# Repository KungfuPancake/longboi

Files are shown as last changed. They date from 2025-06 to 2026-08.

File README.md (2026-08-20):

# Longboi AFC controller
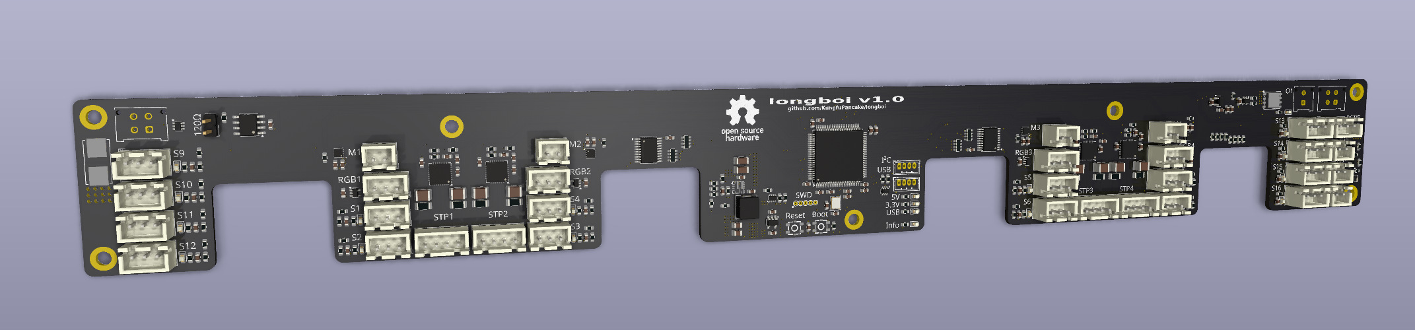
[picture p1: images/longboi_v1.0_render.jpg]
assembled pcb render

Tired of the mess of cables in your BoxTurtle? Want to add a heated filament dryer chamber some time down the road? Want to control that cooling fan with PWM? This project is for you!

The Longboi sits behind the full width of the BoxTurtle front panel and allows very short cable runs of equal length from each respooler and extruder. It's equipped with a beefy STM32H723 MCU and can be controlled with CAN or USB. If using CAN it's also daisy chainable for 8, 12 or even more lanes!

# How to get a Longboi

## Buying a complete board
LDO will sell complete boards via various resellers. Production is currently unknown - check back later for updates!

## PCB + Assembly by JLCPCB
You can order assembled PCBs from pretty much any fab, although currently only production files tested with JLCPCB are available in [jlcpcb/](https://github.com/KungfuPancake/longboi/tree/main/jlcpcb).
To order PCBs with assembly you'll have to go through their manufacturing wizard, using mostly standard settings. Although the JLC engineers will try and correct any mistakes, please do sanity checks on every page.
1. Upload `longboi.zip`into the PCB quote form and select a quantity. Five PCBs is the minimum quantity, cost per board will be lower the more boards you order since most of the cost is setup fees. Select a solder mask color you like - green is usually cheapest. I highly recommend choosing ENIG as a surface finish, HASL is usually not worth the saved money on production boards. Leave all other settings on their default values. Check PCBA (assembly) on the bottom of the form. Click "Next".
2. Check if the PCB looks like it should, then click "Next".
3. Upload `bom.csv` for BOM, `positions.csv`for CPL. Click "Next".
4. Check if all components look right, if there are stock shortages you will have to select replacement. Be very careful to select components that are equal or better in specs. If everything looks good, click "Next".
5. Check the placement of all components, especially if the first pin corresponds with the PCB markings. Slight inaccuracies on the big through hole connectors are okay, as they are hand soldered anyway. Click "Next".
6. You'll see a breakdown of all individual fees and prices. If you're flexible on the amount of PCBs you order you can try and see which amount has the best value to you.
7. Done!

Please be aware that the BOM only contains a fuse holder, the fuses (2410/1808) have to be sourced separately. 4A is a good value to start, depending on the heater you may or may not use the value can be scaled up or down accordingly.

## PCB + assembling it yourself
Order the PCBs anywere you want as the specs are very modest. Assembly of the board is an advanced task requiring lots of soldering, including hot air and/or using a reflow oven. If you don't feel comfortable with that, you should let the fab handle the assembly.

Please be aware that the BOM only contains a fuse holder, the fuses (2410/1808) have to be sourced separately. 4A is a good value to start, depending on the heater you may or may not use the value can be scaled up or down accordingly.

# Preparations
This is a general guideline how to proceed with flashing the Katapult bootloader (optional) and Klipper. If you struggle with the process or encounter errors on the way, especially when using CAN bus, try the detailed instructions and troubleshooting tips and tricks from [Esoterical's CANBus guide](https://canbus.esoterical.online/).
Start with only USB connected via the JST header. When plugging in the USB cable into your computer, the 3.3V and USB LEDs should light up. Now you're ready for flashing!

## CAN
### Katapult
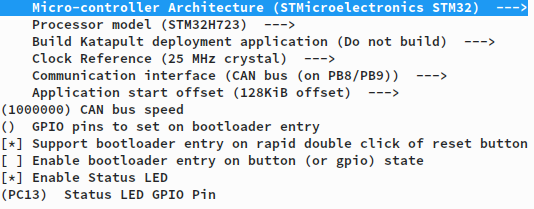
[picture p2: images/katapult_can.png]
katapult reference config for can


### Klipper
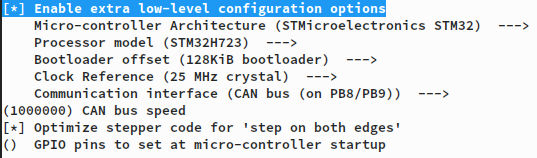
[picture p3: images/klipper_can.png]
klipper reference config for can


## USB
### Katapult
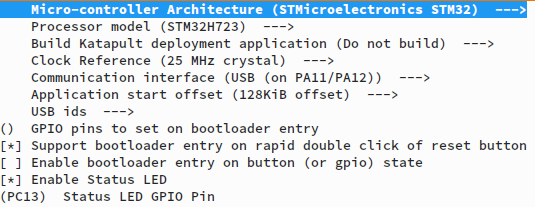
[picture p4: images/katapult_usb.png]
katapult reference config for usb


### Klipper
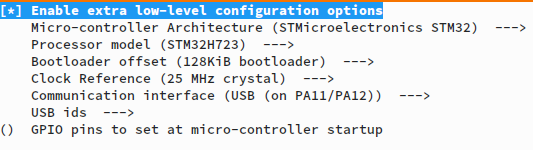
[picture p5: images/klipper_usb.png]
klipper reference config for usb


## Initial flash via DFU
To enable CAN or USB flashing via Katapult or Klipper you'll have to bootstrap the board via the MCUs built-in DFU bootloader, using dfu-util. To enter the DFU bootloader, hold down the "Boot"-button, then press the "Reset"-button shortly. You can now release both buttons and the Longboi should be visible as a "STM Device in DFU Mode" USB device.

Use dfu-util to flash the desired firmware, e.g. Katapult: ```dfu-util -R -a 0 -s 0x08000000:leave -D ~/katapult/out/katapult.bin -d 0483:df11```

## Flashing Katapult and/or Klipper
When using USB, flashing Katapult is not needed as Klipper can update its own firmware. Go through the Klipper build steps using the configuration from above, then flash klipper.bin using dfu-util. From now on you can update Klipper directly with ```make flash FLASH_DEVICE={your device path}```

If you're using a CAN setup and need to use Katapult, build it with the configuration from above and flash it via ```dfu-util```. You may have to reset the board with the "Reset"-button after flashing, the "Info"-LED should be blinking now. If it doesn't, try manually entering Katapult by double-clicking "Reset". Once Katapult is running, all flash operations have to be done via CAN bus. Remove the USB cable from the board and attach it to your CAN bus using a suitable cable. Remember to power down your printer before connecting anything!

If everything went well, Katapult should be visible with the flash tool: ```~/katapult/scripts/flashtool.py -i can0 -q```

You can now flash Klipper: ```~/katapult/scripts/flashtool.py -f ~/klipper/out/klipper.bin -u {your address}```

And you're done!

## Print parts
### Base BoxTurtle
BOM:
* ~95g of primary color filament
* 7x M3x4x5 heat set insert (Voron style)
* 7x M3x10 SHCS
* (Optional) 7x M3x5 brass standoffs
* (Optional) 7x M3x4 SHCS

Print the following parts in your primary color:

* 1x skirt_front_hex_single.stl (no split parts available yet)

If you're not using brass standoffs, also print:

* 7x pcb_spacer_x7.stl

Print all parts using the BoxTurtle settings, make sure that you tuned your filament for shrinkage as the mounting holes won't line up otherwise.

### BoxTurtle Enclosure
Please use the CAD files for reference until a detailed manual is available.

# Assembly
## Mounting PCB + front skirt
### Base BoxTurtle
Add the heat set inserts into the front skirt, then mount the PCB. If you're using brass standoffs, screw those in first, then mount the board using the M3x4 fasteners. If using printed spacers, for easier assembly you can pre-insert two M3x10s into the PCB, add spacers and then mount it on the front skirt. Then use tweezers to add spacers between the PCB and the skirt on the remaining holes and add the rest of the M3x10s.
Insert the front skirt according to the manual and double check that the cutouts on the PCB correspond to the respooler switch tabs.

### BoxTurtle Enclosure
Please use the CAD files for reference until a detailed manual is available.

## Connections
Every respooler + extruder has its own set of connectors on the PCB, e.g. M4, RGB4, S8, S7, STP4.
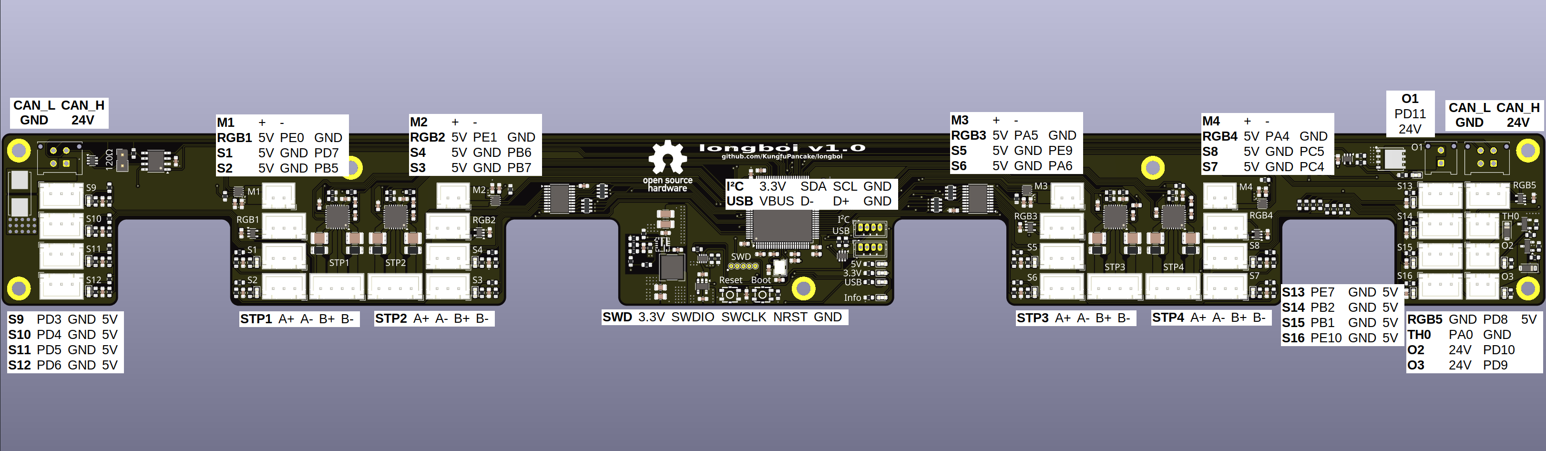
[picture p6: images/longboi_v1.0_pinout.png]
pcb 1.0 render with pinout

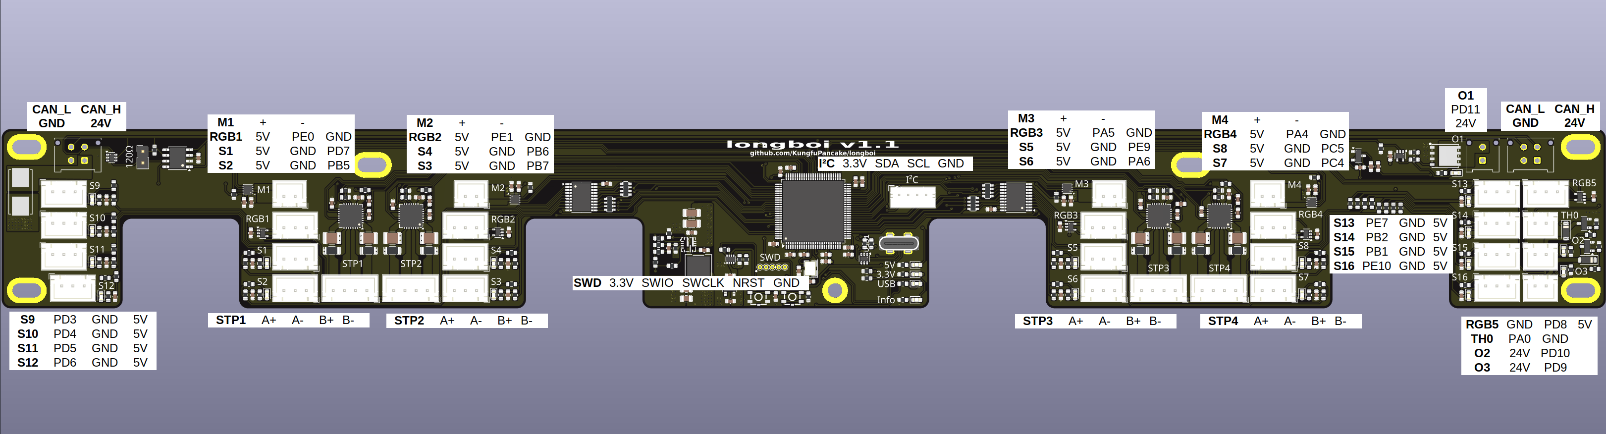
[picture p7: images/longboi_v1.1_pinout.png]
pcb 1.1 render with pinout


If you're making your own cables, to make your life easier, assemble one respooler and one extruder first with generous cable length. Mount everything, measure everything, cut and crimp all connections. Afterwards, remove the respooler and extruder and finish the other three sets outside of the BoxTurtle with your measurements.
Tidy up with cable ties/velcro straps as needed and plug in everything.
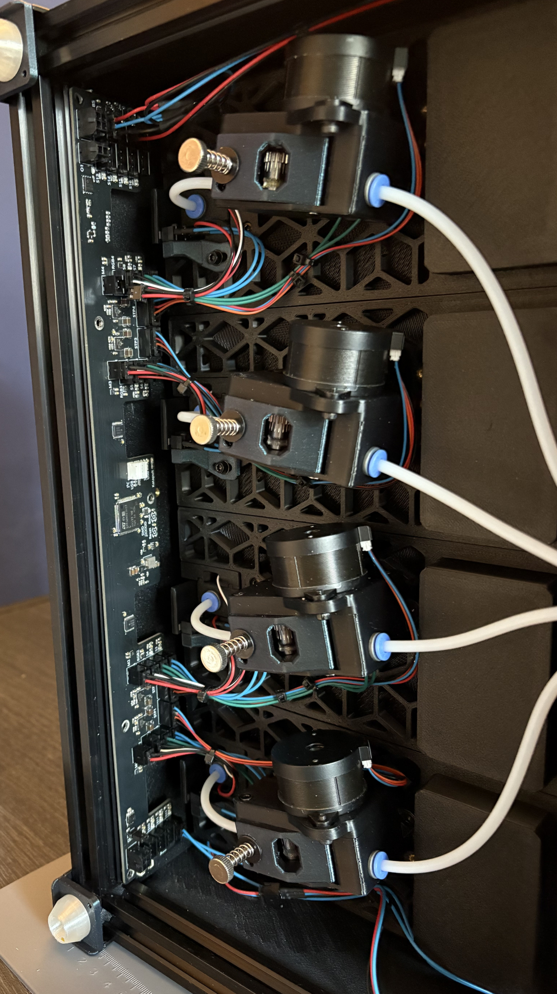
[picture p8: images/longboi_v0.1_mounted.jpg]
mounted pcb


# Configuration
## Pin aliases / longboi.cfg
coming soon
## AFC configuration
coming soon

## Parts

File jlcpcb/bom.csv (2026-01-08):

Designator | Footprint | Quantity | Value | LCSC Part #
C1, C4, C57, C59 | 0603 | 4 | 10uF | C19702
C10, C18, C24, C30, C36, C8 | 0603 | 6 | 2.2uF | C23630
C11, C12, C13, C14, C15, C17, C2, C23, C29, C35, C48, C49, C5, C50, C51, C52, C55, C56, C62, C63, C64, C65, C66, C67, C68, C69, C7, C70, C71, C72, C73, C74, C75, C76, C77, C78, C79, C80, C82, C9 | 0603 | 40 | 100nF | C14663
C16, C22, C28, C34 | 0603 | 4 | 22nF | C21122
C19, C25, C31, C37, C40, C41, C42, C43, C44, C45, C46, C47 | 0603 | 12 | 1uF | C15849
C20, C21, C26, C27, C32, C33, C38, C39 | 1210 | 8 | 47uF | C6120020
C3, C6 | 0603 | 2 | 12pF | C1644
C53, C54 | 1206 | 2 | 10uF | C13585
C58 | 0603 | 1 | 100pF | C14665
C60, C61 | 0805 | 2 | 22uF | C602037
D1 | 0603 | 1 | Blue | C965807
D10, D7 | D_SOD-123 | 2 | 1N4007 | C2902912
D15, D16, D17, D18, D19, D20, D21, D22, D23, D24, D25, D26, D27, D28, D29, D30 | 0603 | 16 | Yellow | C72038
D2, D3, D4 | 0603 | 3 | Green | C2994781
D32 | SOT-23 | 1 | BAV99 | C2500
D5, D6, D9 | 0603 | 3 | Red | C965799
F1 | Fuseholder_Littelfuse_Nano2_154x | 1 | 4A | C108518
J10, J7, J8, J9 | JST_XH_B4B-XH-A_1x04_P2.50mm_Vertical | 4 | Conn_01x04_Pin | C566013
J11, J12, J13, J14, J41, J44, J50 | JST_XH_B2B-XH-A_1x02_P2.50mm_Vertical | 7 | Conn_01x02_Pin | C378939
J15, J16, J17, J18, J23, J24, J25, J26, J27, J28, J29, J30, J31, J32, J33, J34, J35, J36, J37, J38, J40 | JST_XH_B3B-XH-A_1x03_P2.50mm_Vertical | 21 | Conn_01x03_Pin | C565985
J19 | PinHeader_1x02_P2.54mm_Vertical | 1 | Conn_01x02_Pin | C492401
J20, J21 | Molex_Micro-Fit_3.0_43045-0412_2x02_P3.00mm_Vertical | 2 | MX3.0 | C277721
J39 | Molex_Micro-Fit_3.0_43045-0212_2x01_P3.00mm_Vertical | 1 | Conn_01x02_Pin | C293362
J42, J6 | JST_ZH_B4B-ZR_1x04_P1.50mm_Vertical | 2 | JST-ZH | C157997
L1 | L_Chilisin_BMRA00050530 | 1 | L_Ferrite | C7187309
Q1 | DFN-8_L5.9-W5.2-P1.27-LS6.2-BL | 1 | HY1904C2 | C358116
Q2, Q4 | SOT-23 | 2 | IRLML0030 | C67272
R1, R24, R64, R70 | 0603 | 4 | 2.7k | C13167
R10, R11, R4, R5, R6, R7, R8, R9 | 1206 | 8 | 110m | C2934288
R100, R101, R102, R103, R104, R105, R106, R107, R13, R16, R17, R28, R29, R31, R33, R35, R37, R39, R41, R43, R45, R47, R49, R51, R53, R55, R57, R59, R95, R96, R97, R98, R99 | 0603 | 33 | 100k | C14675
R108, R109 | 0603 | 2 | 2.37k | C705759
R110 | 0603 | 1 | 4.7k | C99782
R12 | 0603 | 1 | 120 | C22787
R14 | 0603 | 1 | 56k | C23206
R15 | 0603 | 1 | 0 | C95177
R18, R25, R61, R79, R80, R81, R82, R83, R84, R85, R86, R87, R88, R89, R90, R91, R92, R93, R94 | 0603 | 19 | 3.3k | C22978
R19 | 0603 | 1 | 20k | C2907011
R2, R3 | 0603 | 2 | 15k | C22809
R20, R23, R26, R27, R63, R66, R67, R68, R72 | 0603 | 9 | 10k | C98220
R21 | 0603 | 1 | 49.9 | C114625
R22 | 0603 | 1 | 73.2k | C14890
R30, R32, R34, R36, R38, R40, R42, R44, R46, R48, R50, R52, R54, R56, R58, R60, R62, R65, R71 | 0603 | 19 | 100 | C105588
RN1, RN2, RN3, RN4 | R_Array_Convex_4x0603 | 4 | 10k | C29718
SW1, SW2 | SW-SMD_4P-L3.4-W3.4-P2.00-LS4.0_TS3315A160GF | 2 | SW_SPST | C557593
U1 | LQFP-100_14x14mm_P0.5mm | 1 | STM32H723VGTx | C730142
U10, U11, U8, U9 | WSON-8-1EP_2x2mm_P0.5mm_EP0.9x1.6mm | 4 | DRV8837 | C39159
U12, U13, U14, U15, U21, U22 | SOT-353_SC-70-5 | 6 | 74LVC1G126 | C7394032
U16 | SOIC-8_3.9x4.9mm_P1.27mm | 1 | SN65HVD231 | C129257
U17 | SOT-583-8 | 1 | TPS2116DRL | C3235557
U18 | VQFN-HR-10_L3.0-W3.0_RPA | 1 | TPS56637RPAR | C841386
U19 | SOT-23-5 | 1 | ME6211C33M5 | C82942
U2, U3 | TSSOP-20_4.4x6.5mm_P0.65mm | 2 | SN74LVC245APW | C7848
U20, U23 | SOT-363_SC-70-6 | 2 | SMF05CT1G-ES | C5180312
U4, U5, U6, U7 | QFN-28-1EP_5x5mm_P0.5mm_EP3.75x3.75mm_ThermalVias | 4 | TMC2209-LA | C2150710
Y1 | Crystal_SMD_3225-4Pin_3.2x2.5mm | 1 | 25MHz | C9006

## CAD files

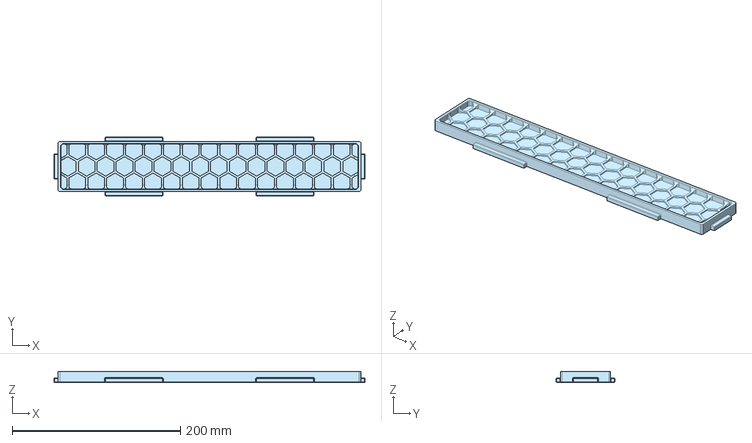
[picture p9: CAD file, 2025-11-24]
cad/bt/skirt_front_hex_single.step
370.0 x 69.6 x 12.5 mm

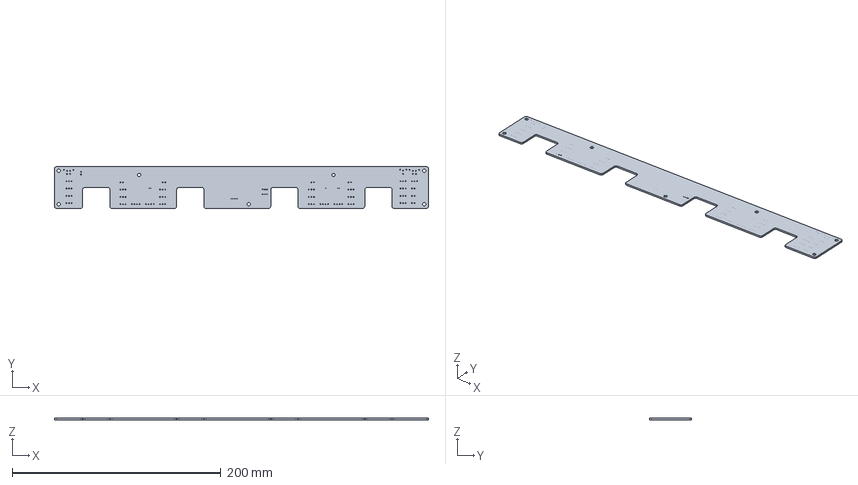
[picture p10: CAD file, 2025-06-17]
pcb/longboi.step
358.0 x 40.0 x 1.51 mm

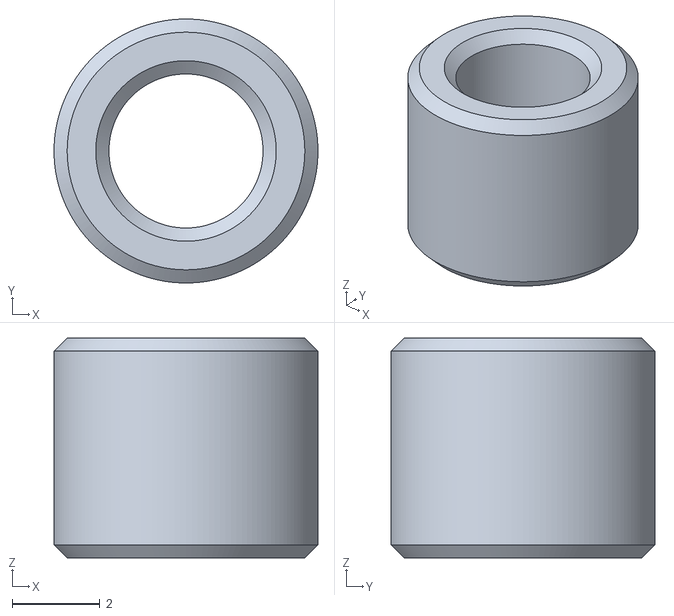
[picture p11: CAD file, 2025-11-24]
stl/bt/pcb_spacer_x7.stl
6.00 x 6.00 x 5.00

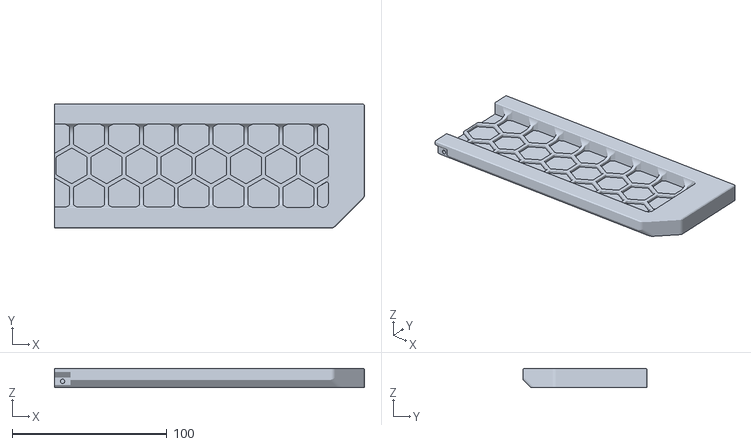
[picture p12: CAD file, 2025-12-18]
stl/bte/hex_front_right.stl
200.0 x 80.0 x 12.5

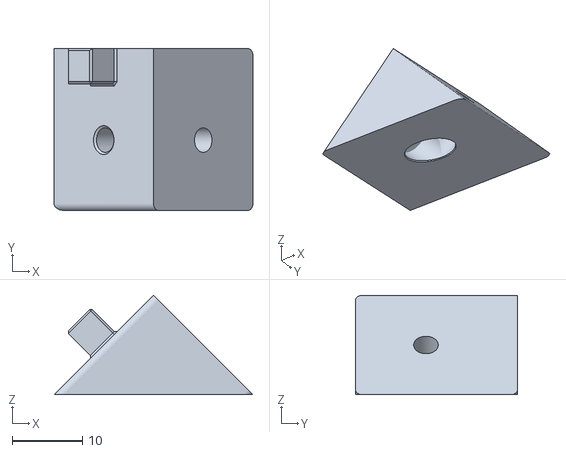
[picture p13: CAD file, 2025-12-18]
stl/bte/side_lower_left.stl
28.3 x 23.0 x 14.1

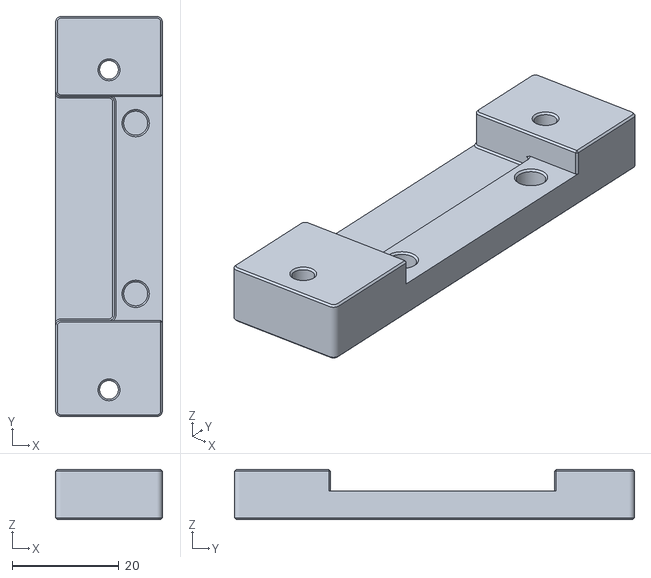
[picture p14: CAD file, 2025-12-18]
stl/bte/spacer_left.stl
20.0 x 75.0 x 9.40

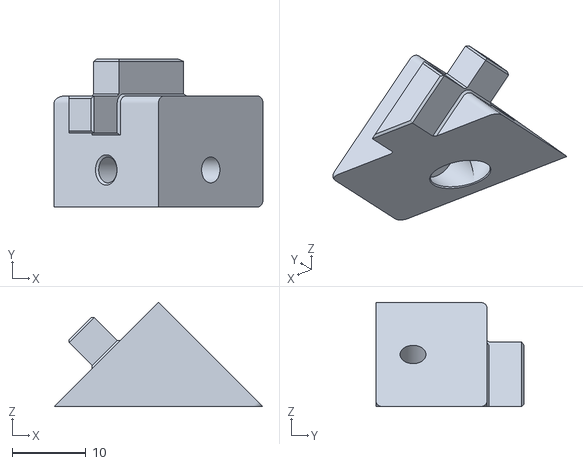
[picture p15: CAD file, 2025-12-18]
stl/bte/side_upper_left.stl
28.3 x 20.0 x 14.1

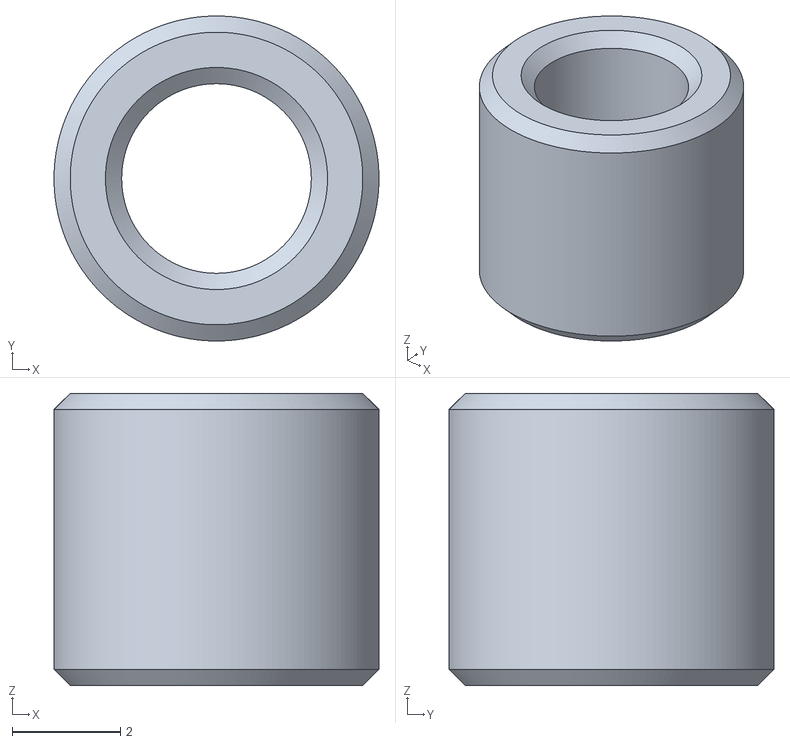
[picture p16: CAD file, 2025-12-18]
stl/bte/pcb_spacer_x3.stl
6.00 x 6.00 x 5.40

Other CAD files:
cad/bt/pcb_spacer.step
stl/bte/spacer_right.stl
stl/bte/hex_front_left.stl
stl/bte/side_lower_right.stl
stl/bte/side_upper_right.stl
stl/bt/skirt_front_hex_single.stl

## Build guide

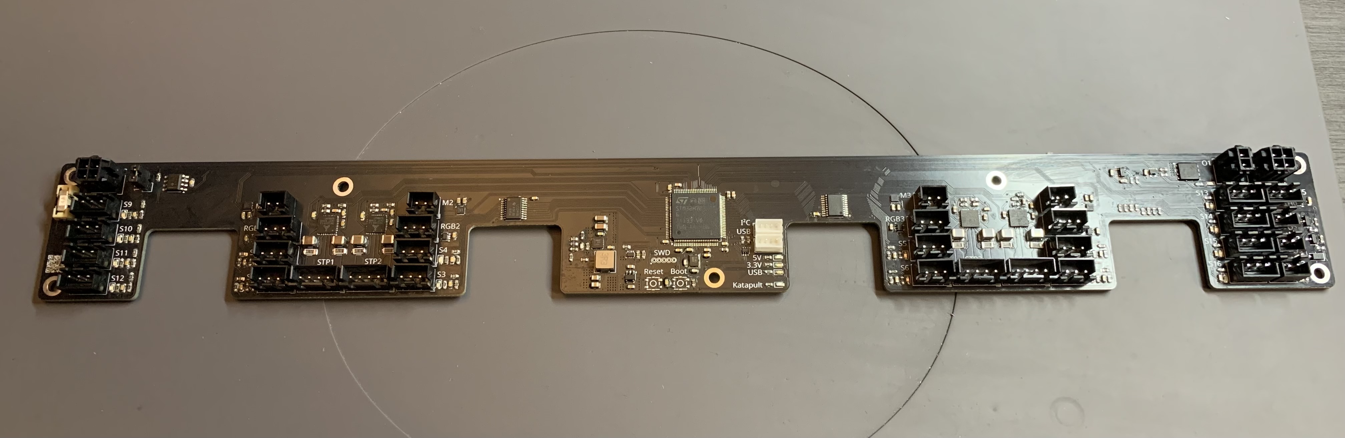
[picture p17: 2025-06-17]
images/longboi_v0.1_assembled.jpg

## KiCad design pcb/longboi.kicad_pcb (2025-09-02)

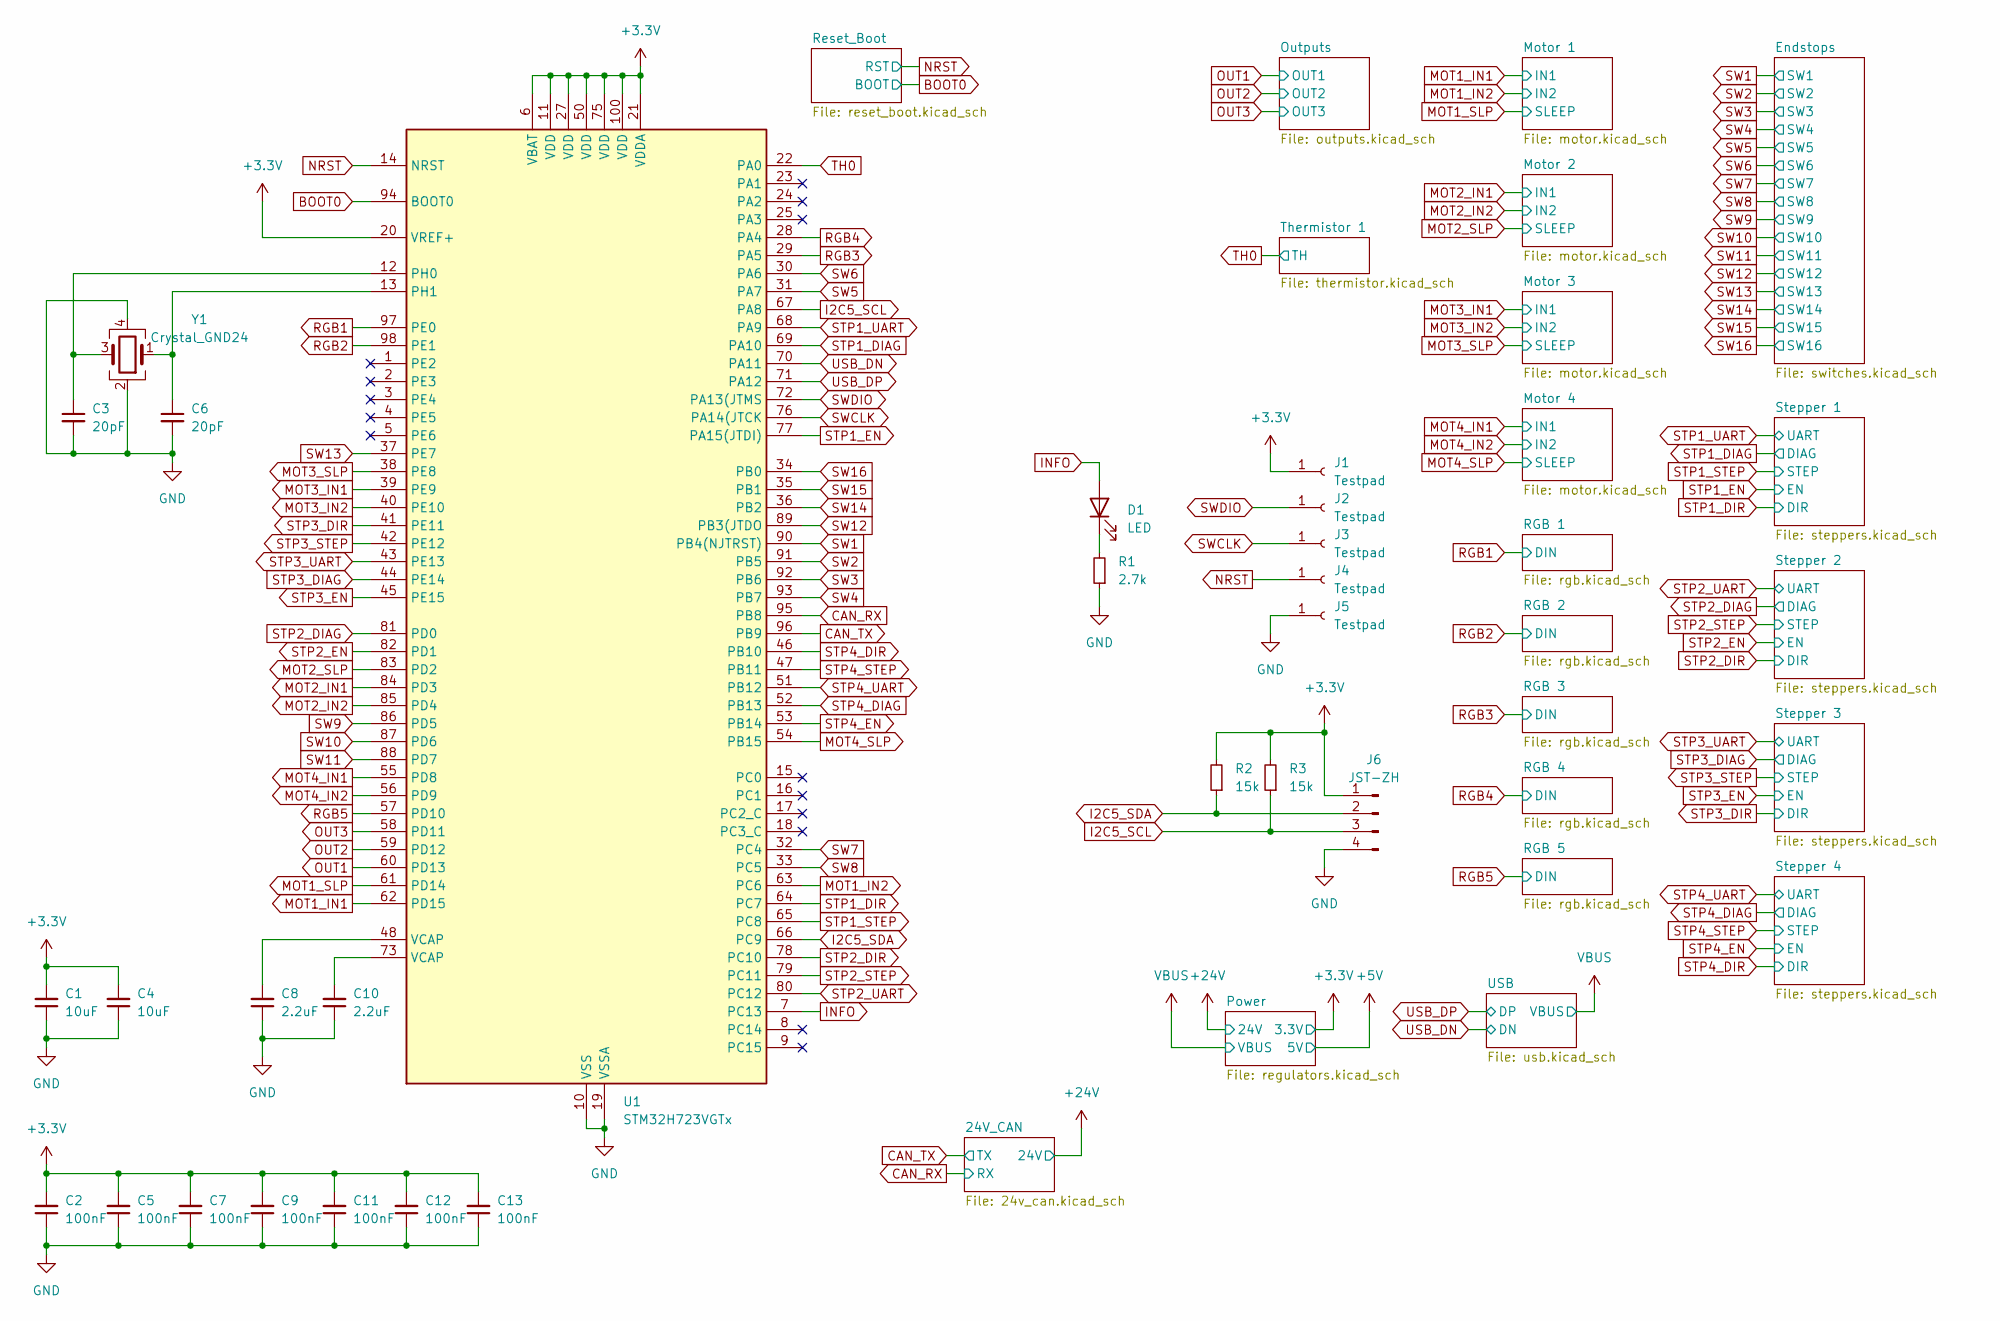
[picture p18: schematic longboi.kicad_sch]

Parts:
C1, C4: 10uF; C_0603_1608Metric
C2, C5, C7, C9, C11, C12, C13: 100nF; C_0603_1608Metric
C3, C6: 20pF; C_0603_1608Metric
C8, C10: 2.2uF; C_0603_1608Metric
D1: LED; LED_0603_1608Metric
J1, J2, J3, J4, J5: Testpad; TestPoint_THTPad_D1.0mm_Drill0.5mm
J6: JST-ZH; JST_ZH_B4B-ZR_1x04_P1.50mm_Vertical
R1: 2.7k; R_0603_1608Metric
R2, R3: 15k; R_0603_1608Metric
U1: STM32H723VGTx; LQFP-100_14x14mm_P0.5mm
Y1: Crystal_GND24; Crystal_SMD_3225-4Pin_3.2x2.5mm

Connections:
+3.3V: C1.2, C2.2, C4.2, C5.2, C7.2, C9.2, C11.2, C12.2, C13.2, J1.1, J6.1, R2.2, R3.2, U1.6 (VBAT), U1.11 (VDD), U1.20 (VREF+), U1.21 (VDDA), U1.27 (VDD), U1.50 (VDD), U1.75 (VDD), U1.100 (VDD); also elsewhere on the board
BOOT0: U1.94 (BOOT0); also elsewhere on the board
CAN_RX: U1.95 (PB8); also elsewhere on the board
CAN_TX: U1.96 (PB9); also elsewhere on the board
GND: C1.1, C2.1, C3.2, C4.1, C5.1, C6.2, C7.1, C8.1, C9.1, C10.1, C11.1, C12.1, C13.1, J5.1, J6.4, R1.1, U1.10 (VSS), U1.19 (VSSA), U1.26 (VSS), U1.49 (VSS), U1.74 (VSS), U1.99 (VSS), Y1.2, Y1.4; also elsewhere on the board
I2C5_SCL: J6.3, R3.1, U1.67 (PA8)
I2C5_SDA: J6.2, R2.1, U1.66 (PC9)
INFO: D1.2 (A), U1.7 (PC13)
MOT1_IN1: U1.62 (PD15); also elsewhere on the board
MOT1_IN2: U1.63 (PC6); also elsewhere on the board
MOT1_SLP: U1.61 (PD14); also elsewhere on the board
MOT2_IN1: U1.84 (PD3); also elsewhere on the board
MOT2_IN2: U1.85 (PD4); also elsewhere on the board
MOT2_SLP: U1.83 (PD2); also elsewhere on the board
MOT3_IN1: U1.39 (PE9); also elsewhere on the board
MOT3_IN2: U1.40 (PE10); also elsewhere on the board
MOT3_SLP: U1.38 (PE8); also elsewhere on the board
MOT4_IN1: U1.55 (PD8); also elsewhere on the board
MOT4_IN2: U1.56 (PD9); also elsewhere on the board
MOT4_SLP: U1.54 (PB15); also elsewhere on the board
NRST: J4.1, U1.14 (NRST); also elsewhere on the board
unnamed: C8.2, U1.48 (VCAP)
unnamed: C10.2, U1.73 (VCAP)
unnamed: D1.1 (K), R1.2
unnamed: C3.1, U1.12 (PH0), Y1.3
unnamed: C6.1, U1.13 (PH1), Y1.1
OUT1: U1.60 (PD13); also elsewhere on the board
OUT2: U1.59 (PD12); also elsewhere on the board
OUT3: U1.58 (PD11); also elsewhere on the board
RGB1: U1.97 (PE0); also elsewhere on the board
RGB2: U1.98 (PE1); also elsewhere on the board
RGB3: U1.29 (PA5); also elsewhere on the board
RGB4: U1.28 (PA4); also elsewhere on the board
RGB5: U1.57 (PD10); also elsewhere on the board
STP1_DIAG: U1.69 (PA10); also elsewhere on the board
STP1_DIR: U1.64 (PC7); also elsewhere on the board
STP1_EN: U1.77 (PA15(JTDI)); also elsewhere on the board
STP1_STEP: U1.65 (PC8); also elsewhere on the board
STP1_UART: U1.68 (PA9); also elsewhere on the board
STP2_DIAG: U1.81 (PD0); also elsewhere on the board
STP2_DIR: U1.78 (PC10); also elsewhere on the board
STP2_EN: U1.82 (PD1); also elsewhere on the board
STP2_STEP: U1.79 (PC11); also elsewhere on the board
STP2_UART: U1.80 (PC12); also elsewhere on the board
STP3_DIAG: U1.44 (PE14); also elsewhere on the board
STP3_DIR: U1.41 (PE11); also elsewhere on the board
STP3_EN: U1.45 (PE15); also elsewhere on the board
STP3_STEP: U1.42 (PE12); also elsewhere on the board
STP3_UART: U1.43 (PE13); also elsewhere on the board
STP4_DIAG: U1.52 (PB13); also elsewhere on the board
STP4_DIR: U1.46 (PB10); also elsewhere on the board
STP4_EN: U1.53 (PB14); also elsewhere on the board
STP4_STEP: U1.47 (PB11); also elsewhere on the board
STP4_UART: U1.51 (PB12); also elsewhere on the board
SW1: U1.90 (PB4(NJTRST)); also elsewhere on the board
SW2: U1.91 (PB5); also elsewhere on the board
SW3: U1.92 (PB6); also elsewhere on the board
SW4: U1.93 (PB7); also elsewhere on the board
SW5: U1.31 (PA7); also elsewhere on the board
SW6: U1.30 (PA6); also elsewhere on the board
SW7: U1.32 (PC4); also elsewhere on the board
SW8: U1.33 (PC5); also elsewhere on the board
SW9: U1.86 (PD5); also elsewhere on the board
SW10: U1.87 (PD6); also elsewhere on the board
SW11: U1.88 (PD7); also elsewhere on the board
SW12: U1.89 (PB3(JTDO); also elsewhere on the board
SW13: U1.37 (PE7); also elsewhere on the board
SW14: U1.36 (PB2); also elsewhere on the board
SW15: U1.35 (PB1); also elsewhere on the board
SW16: U1.34 (PB0); also elsewhere on the board
SWCLK: J3.1, U1.76 (PA14(JTCK)
SWDIO: J2.1, U1.72 (PA13(JTMS)
TH0: U1.22 (PA0); also elsewhere on the board
USB_DN: U1.70 (PA11); also elsewhere on the board
USB_DP: U1.71 (PA12); also elsewhere on the board

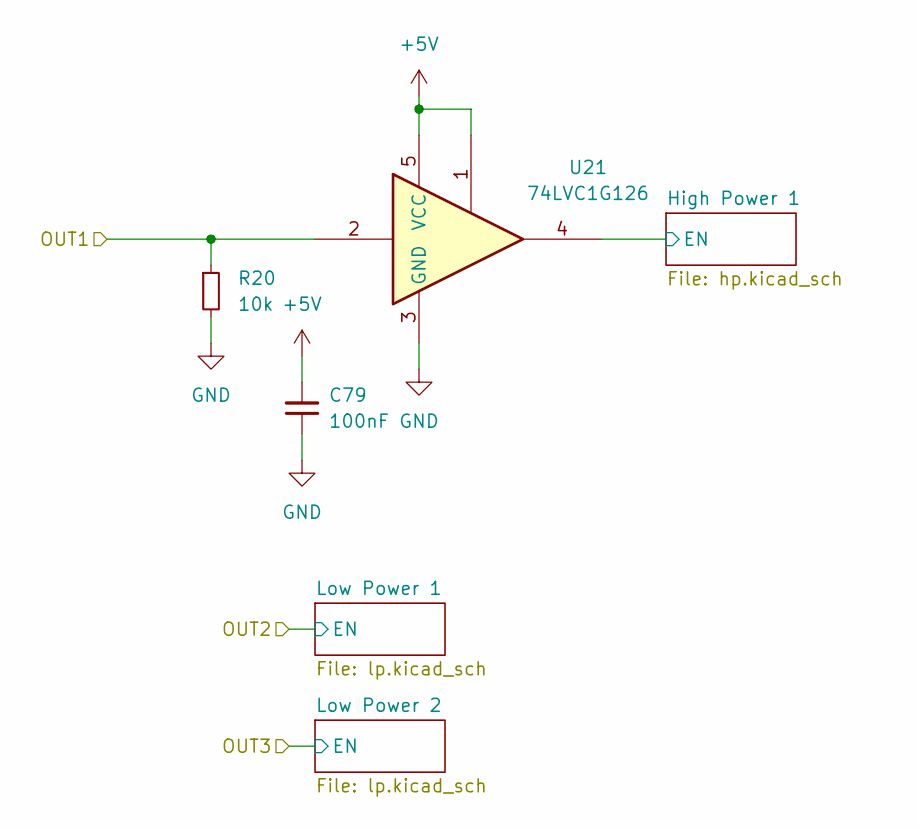
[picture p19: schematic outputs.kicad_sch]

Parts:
C79: 100nF; C_0603_1608Metric
R20: 10k; R_0603_1608Metric
U21: 74LVC1G126; SOT-353_SC-70-5

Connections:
+5V: C79.2, U21.1, U21.5 (VCC); also elsewhere on the board
/Outputs/High Power 1/EN: U21.4; also elsewhere on the board
GND: C79.1, R20.2, U21.3 (GND); also elsewhere on the board
OUT1: R20.1, U21.2; also elsewhere on the board

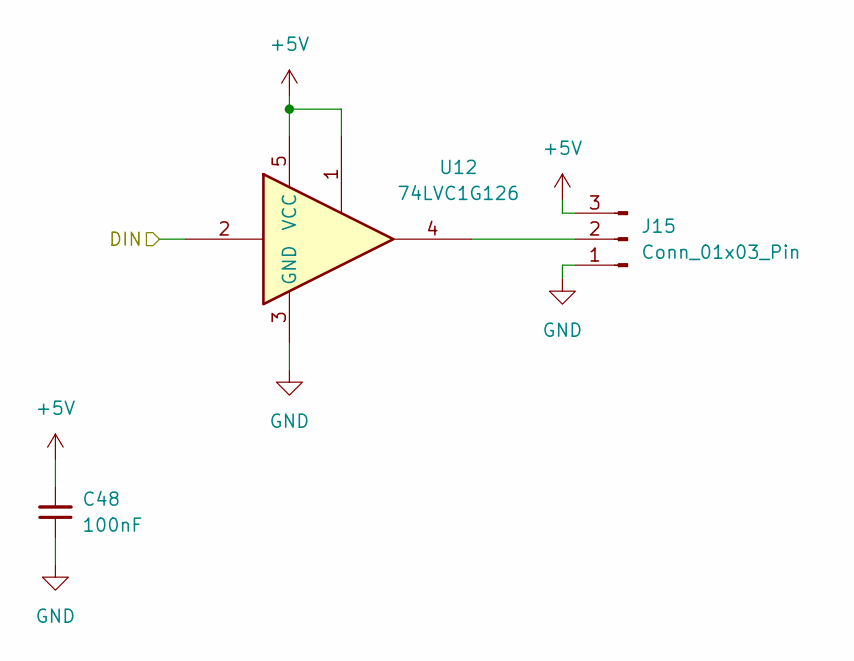
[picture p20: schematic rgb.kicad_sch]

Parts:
C48: 100nF; C_0603_1608Metric
J15: Conn_01x03_Pin; JST_XH_B3B-XH-A_1x03_P2.50mm_Vertical
U12: 74LVC1G126; SOT-353_SC-70-5

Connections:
+5V: C48.2, J15.3, U12.1, U12.5 (VCC); also elsewhere on the board
GND: C48.1, J15.1, U12.3 (GND); also elsewhere on the board
unnamed: J15.2, U12.4
RGB1: U12.2; also elsewhere on the board

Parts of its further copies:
C49, C50, C51, C80: 100nF; C_0603_1608Metric
J16, J17, J18, J40: Conn_01x03_Pin; JST_XH_B3B-XH-A_1x03_P2.50mm_Vertical
U13, U14, U15, U22: 74LVC1G126; SOT-353_SC-70-5

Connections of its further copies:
+5V: C49.2, C50.2, C51.2, C80.2, J16.3, J17.3, J18.3, J40.3, U13.1, U13.5 (VCC), U14.1, U14.5 (VCC), U15.1, U15.5 (VCC), U22.1, U22.5 (VCC); also elsewhere on the board
GND: C49.1, C50.1, C51.1, C80.1, J16.1, J17.1, J18.1, J40.1, U13.3 (GND), U14.3 (GND), U15.3 (GND), U22.3 (GND); also elsewhere on the board
unnamed: J16.2, U13.4
unnamed: J17.2, U14.4
unnamed: J18.2, U15.4
unnamed: J40.2, U22.4
RGB2: U13.2; also elsewhere on the board
RGB3: U14.2; also elsewhere on the board
RGB4: U15.2; also elsewhere on the board
RGB5: U22.2; also elsewhere on the board

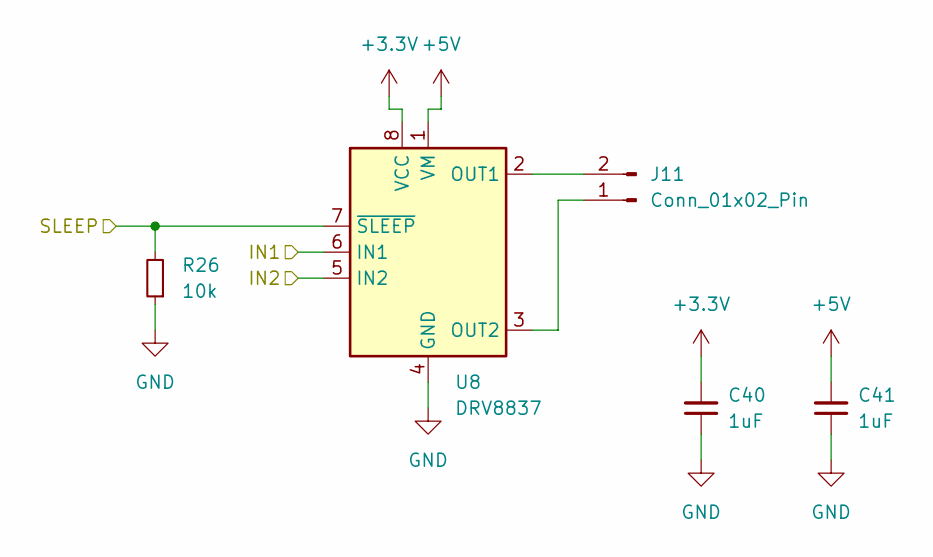
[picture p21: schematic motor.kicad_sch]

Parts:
C40, C41: 1uF; C_0603_1608Metric
J11: Conn_01x02_Pin; JST_XH_B2B-XH-A_1x02_P2.50mm_Vertical
R26: 10k; R_0603_1608Metric
U8: DRV8837; WSON-8-1EP_2x2mm_P0.5mm_EP0.9x1.6mm

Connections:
+3.3V: C40.2, U8.8 (VCC); also elsewhere on the board
+5V: C41.2, U8.1 (VM); also elsewhere on the board
GND: C40.1, C41.1, R26.1, U8.4 (GND), U8.9 (GND); also elsewhere on the board
MOT1_IN1: U8.6 (IN1); also elsewhere on the board
MOT1_IN2: U8.5 (IN2); also elsewhere on the board
MOT1_SLP: R26.2, U8.7 (~SLEEP); also elsewhere on the board
unnamed: J11.1, U8.3 (OUT2)
unnamed: J11.2, U8.2 (OUT1)

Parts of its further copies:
C42, C43, C44, C45, C46, C47: 1uF; C_0603_1608Metric
J12, J13, J14: Conn_01x02_Pin; JST_XH_B2B-XH-A_1x02_P2.50mm_Vertical
R27, R67, R68: 10k; R_0603_1608Metric
U9, U10, U11: DRV8837; WSON-8-1EP_2x2mm_P0.5mm_EP0.9x1.6mm

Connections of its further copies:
+3.3V: C42.2, C44.2, C46.2, U9.8 (VCC), U10.8 (VCC), U11.8 (VCC); also elsewhere on the board
+5V: C43.2, C45.2, C47.2, U9.1 (VM), U10.1 (VM), U11.1 (VM); also elsewhere on the board
GND: C42.1, C43.1, C44.1, C45.1, C46.1, C47.1, R27.1, R67.1, R68.1, U9.4 (GND), U9.9 (GND), U10.4 (GND), U10.9 (GND), U11.4 (GND), U11.9 (GND); also elsewhere on the board
MOT2_IN1: U9.6 (IN1); also elsewhere on the board
MOT2_IN2: U9.5 (IN2); also elsewhere on the board
MOT2_SLP: R27.2, U9.7 (~SLEEP); also elsewhere on the board
MOT3_IN1: U10.6 (IN1); also elsewhere on the board
MOT3_IN2: U10.5 (IN2); also elsewhere on the board
MOT3_SLP: R67.2, U10.7 (~SLEEP); also elsewhere on the board
MOT4_IN1: U11.6 (IN1); also elsewhere on the board
MOT4_IN2: U11.5 (IN2); also elsewhere on the board
MOT4_SLP: R68.2, U11.7 (~SLEEP); also elsewhere on the board
unnamed: J12.1, U9.3 (OUT2)
unnamed: J12.2, U9.2 (OUT1)
unnamed: J13.1, U10.3 (OUT2)
unnamed: J13.2, U10.2 (OUT1)
unnamed: J14.1, U11.3 (OUT2)
unnamed: J14.2, U11.2 (OUT1)

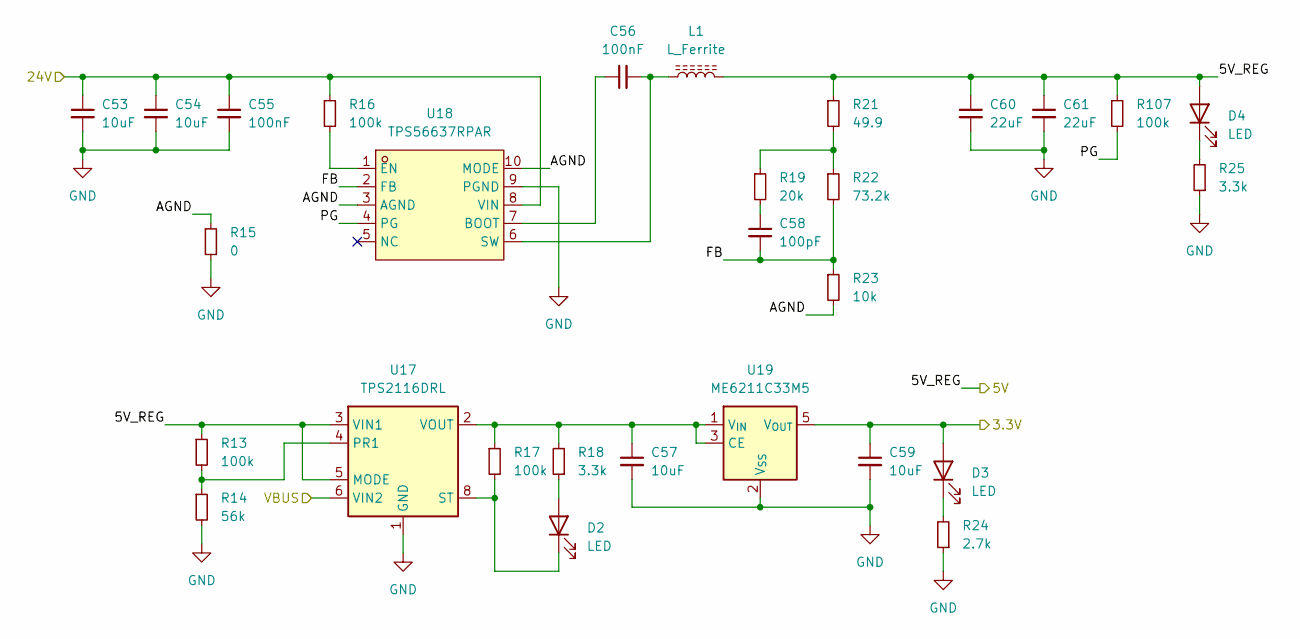
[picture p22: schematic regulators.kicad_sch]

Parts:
C53, C54: 10uF; C_1206_3216Metric
C55, C56: 100nF; C_0603_1608Metric
C57, C59: 10uF; C_0603_1608Metric
C58: 100pF; C_0603_1608Metric
C60, C61: 22uF; C_0805_2012Metric
D2, D3, D4: LED; LED_0603_1608Metric
L1: L_Ferrite; L_Chilisin_BMRA00050530
R13, R16, R17, R107: 100k; R_0603_1608Metric
R14: 56k; R_0603_1608Metric
R15: 0; R_0603_1608Metric
R18, R25: 3.3k; R_0603_1608Metric
R19: 20k; R_0603_1608Metric
R21: 49.9; R_0603_1608Metric
R22: 73.2k; R_0603_1608Metric
R23: 10k; R_0603_1608Metric
R24: 2.7k; R_0603_1608Metric
U17: TPS2116DRL; SOT-583-8
U18: TPS56637RPAR; VQFN-HR-10_L3.0-W3.0_RPA; LCSC Part C841386
U19: ME6211C33M5; SOT-23-5

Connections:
+3.3V: C59.1, D3.2 (A), U19.5 (V_{OUT}); also elsewhere on the board
+5V: C60.1, C61.1, D4.2 (A), L1.2, R13.1, R21.1, R107.1, U17.3 (VIN1), U17.5 (MODE); also elsewhere on the board
+24V: C53.1, C54.1, C55.1, R16.1, U18.8 (VIN); also elsewhere on the board
/Power/AGND: R15.1, R23.2, U18.3 (AGND), U18.10 (MODE)
/Power/FB: C58.2, R22.2, R23.1, U18.2 (FB)
/Power/PG: R107.2, U18.4 (PG)
GND: C53.2, C54.2, C55.2, C57.2, C59.2, C60.2, C61.2, R14.2, R15.2, R24.1, R25.1, U17.1 (GND), U18.9 (PGND), U19.2 (V_{SS}); also elsewhere on the board
unnamed: C58.1, R19.2
unnamed: D2.2 (A), R18.1
unnamed: D2.1 (K), R17.2, U17.8 (ST)
unnamed: D3.1 (K), R24.2
unnamed: D4.1 (K), R25.2
unnamed: R19.1, R21.2, R22.1
unnamed: R13.2, R14.1, U17.4 (PR1)
unnamed: C56.1, U18.7 (BOOT)
unnamed: R16.2, U18.1 (EN)
unnamed: C56.2, L1.1, U18.6 (SW)
unnamed: C57.1, R17.1, R18.2, U17.2 (VOUT), U17.7 (VOUT), U19.1 (V_{IN}), U19.3 (CE)
VBUS: U17.6 (VIN2); also elsewhere on the board

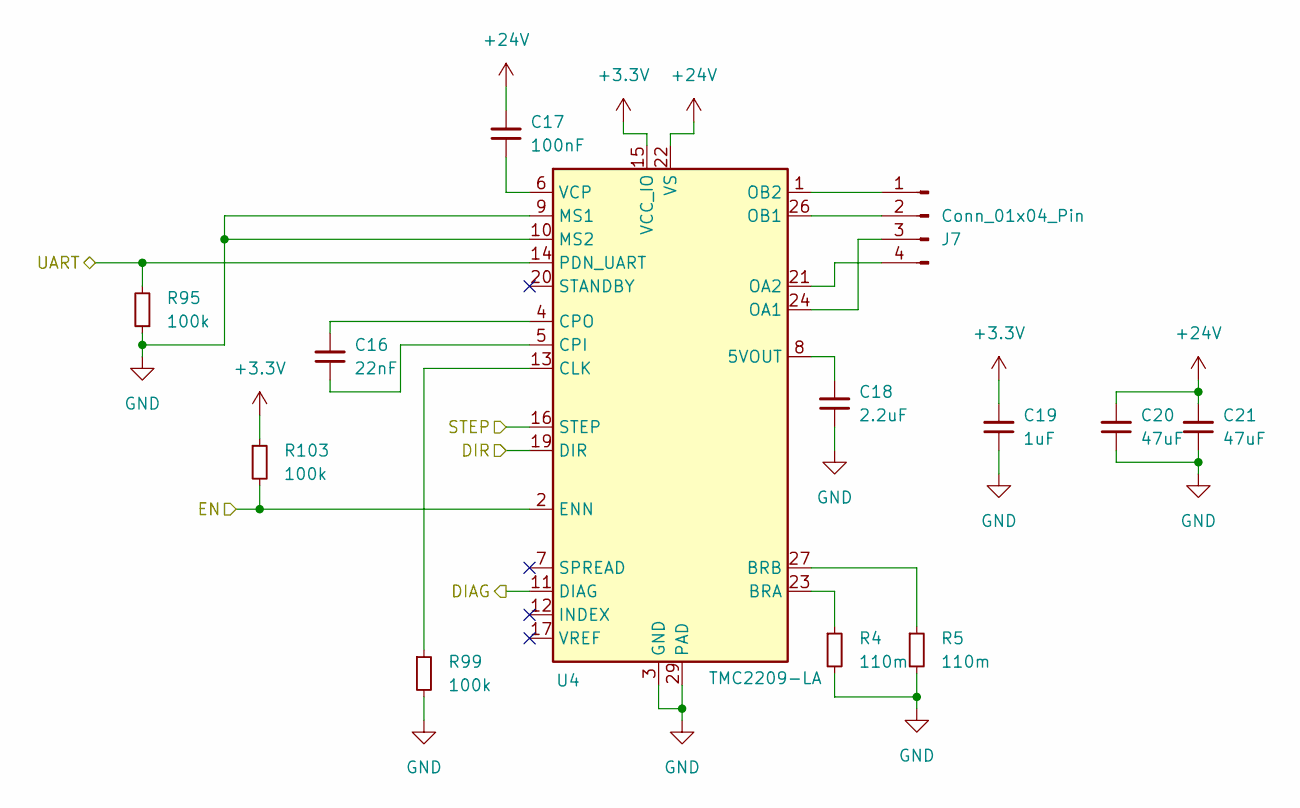
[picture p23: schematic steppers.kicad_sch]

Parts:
C16: 22nF; C_0603_1608Metric
C17: 100nF; C_0603_1608Metric
C18: 2.2uF; C_0603_1608Metric
C19: 1uF; C_0603_1608Metric
C20, C21: 47uF; C_1210_3225Metric
J7: Conn_01x04_Pin; JST_XH_B4B-XH-A_1x04_P2.50mm_Vertical
R4, R5: 110m; R_1206_3216Metric
R95, R99, R103: 100k; R_0603_1608Metric
U4: TMC2209-LA; QFN-28-1EP_5x5mm_P0.5mm_EP3.75x3.75mm_ThermalVias

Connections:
+3.3V: C19.2, R103.1, U4.15 (VCC_IO); also elsewhere on the board
+24V: C17.2, C20.2, C21.2, U4.22 (VS), U4.28 (VS); also elsewhere on the board
GND: C18.1, C19.1, C20.1, C21.1, R4.2, R5.2, R95.1, R99.2, U4.3 (GND), U4.9 (MS1), U4.10 (MS2), U4.18 (GND), U4.29 (PAD); also elsewhere on the board
unnamed: J7.1, U4.1 (OB2)
unnamed: J7.2, U4.26 (OB1)
unnamed: J7.3, U4.24 (OA1)
unnamed: J7.4, U4.21 (OA2)
unnamed: C18.2, U4.8 (5VOUT)
unnamed: R4.1, U4.23 (BRA)
unnamed: R5.1, U4.27 (BRB)
unnamed: R99.1, U4.13 (CLK)
unnamed: C16.1, U4.5 (CPI)
unnamed: C16.2, U4.4 (CPO)
unnamed: C17.1, U4.6 (VCP)
STP1_DIAG: U4.11 (DIAG); also elsewhere on the board
STP1_DIR: U4.19 (DIR); also elsewhere on the board
STP1_EN: R103.2, U4.2 (ENN); also elsewhere on the board
STP1_STEP: U4.16 (STEP); also elsewhere on the board
STP1_UART: R95.2, U4.14 (PDN_UART); also elsewhere on the board

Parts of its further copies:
C22, C28, C34: 22nF; C_0603_1608Metric
C23, C29, C35: 100nF; C_0603_1608Metric
C24, C30, C36: 2.2uF; C_0603_1608Metric
C25, C31, C37: 1uF; C_0603_1608Metric
C26, C27, C32, C33, C38, C39: 47uF; C_1210_3225Metric
J8, J9, J10: Conn_01x04_Pin; JST_XH_B4B-XH-A_1x04_P2.50mm_Vertical
R6, R7, R8, R9, R10, R11: 110m; R_1206_3216Metric
R96, R97, R98, R100, R101, R102, R104, R105, R106: 100k; R_0603_1608Metric
U5, U6, U7: TMC2209-LA; QFN-28-1EP_5x5mm_P0.5mm_EP3.75x3.75mm_ThermalVias

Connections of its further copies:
+3.3V: C25.2, C31.2, C37.2, R104.1, R105.1, R106.1, U5.15 (VCC_IO), U6.15 (VCC_IO), U7.15 (VCC_IO); also elsewhere on the board
+24V: C23.2, C26.2, C27.2, C29.2, C32.2, C33.2, C35.2, C38.2, C39.2, U5.22 (VS), U5.28 (VS), U6.22 (VS), U6.28 (VS), U7.22 (VS), U7.28 (VS); also elsewhere on the board
GND: C24.1, C25.1, C26.1, C27.1, C30.1, C31.1, C32.1, C33.1, C36.1, C37.1, C38.1, C39.1, R6.2, R7.2, R8.2, R9.2, R10.2, R11.2, R96.1, R97.1, R98.1, R100.2, R101.2, R102.2, U5.3 (GND), U5.9 (MS1), U5.10 (MS2), U5.18 (GND), U5.29 (PAD), U6.3 (GND), U6.9 (MS1), U6.10 (MS2), U6.18 (GND), U6.29 (PAD), U7.3 (GND), U7.9 (MS1), U7.10 (MS2), U7.18 (GND), U7.29 (PAD); also elsewhere on the board
unnamed: J8.1, U5.1 (OB2)
unnamed: J8.2, U5.26 (OB1)
unnamed: J8.3, U5.24 (OA1)
unnamed: J8.4, U5.21 (OA2)
unnamed: J9.1, U6.1 (OB2)
unnamed: J9.2, U6.26 (OB1)
unnamed: J9.3, U6.24 (OA1)
unnamed: J9.4, U6.21 (OA2)
unnamed: J10.1, U7.1 (OB2)
unnamed: J10.2, U7.26 (OB1)
unnamed: J10.3, U7.24 (OA1)
unnamed: J10.4, U7.21 (OA2)
unnamed: C24.2, U5.8 (5VOUT)
unnamed: R6.1, U5.23 (BRA)
unnamed: R7.1, U5.27 (BRB)
unnamed: R100.1, U5.13 (CLK)
unnamed: C22.1, U5.5 (CPI)
unnamed: C22.2, U5.4 (CPO)
unnamed: C23.1, U5.6 (VCP)
unnamed: C30.2, U6.8 (5VOUT)
unnamed: R8.1, U6.23 (BRA)
unnamed: R9.1, U6.27 (BRB)
unnamed: R101.1, U6.13 (CLK)
unnamed: C28.1, U6.5 (CPI)
unnamed: C28.2, U6.4 (CPO)
unnamed: C29.1, U6.6 (VCP)
unnamed: C36.2, U7.8 (5VOUT)
unnamed: R10.1, U7.23 (BRA)
unnamed: R11.1, U7.27 (BRB)
unnamed: R102.1, U7.13 (CLK)
unnamed: C34.1, U7.5 (CPI)
unnamed: C34.2, U7.4 (CPO)
unnamed: C35.1, U7.6 (VCP)
STP2_DIAG: U5.11 (DIAG); also elsewhere on the board
STP2_DIR: U5.19 (DIR); also elsewhere on the board
STP2_EN: R104.2, U5.2 (ENN); also elsewhere on the board
STP2_STEP: U5.16 (STEP); also elsewhere on the board
STP2_UART: R96.2, U5.14 (PDN_UART); also elsewhere on the board
STP3_DIAG: U6.11 (DIAG); also elsewhere on the board
STP3_DIR: U6.19 (DIR); also elsewhere on the board
STP3_EN: R105.2, U6.2 (ENN); also elsewhere on the board
STP3_STEP: U6.16 (STEP); also elsewhere on the board
STP3_UART: R97.2, U6.14 (PDN_UART); also elsewhere on the board
STP4_DIAG: U7.11 (DIAG); also elsewhere on the board
STP4_DIR: U7.19 (DIR); also elsewhere on the board
STP4_EN: R106.2, U7.2 (ENN); also elsewhere on the board
STP4_STEP: U7.16 (STEP); also elsewhere on the board
STP4_UART: R98.2, U7.14 (PDN_UART); also elsewhere on the board

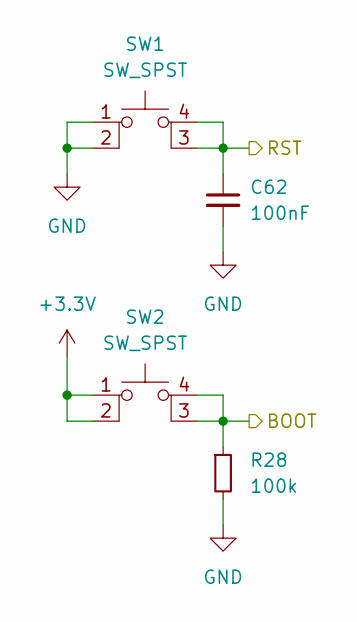
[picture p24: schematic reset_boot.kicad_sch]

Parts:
C62: 100nF; C_0603_1608Metric
R28: 100k; R_0603_1608Metric
SW1, SW2: SW_SPST; SW-SMD_4P-L3.4-W3.4-P2.00-LS4.0_TS3315A160GF

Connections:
+3.3V: SW2.1, SW2.2; also elsewhere on the board
BOOT0: R28.1, SW2.3 (K), SW2.4 (A); also elsewhere on the board
GND: C62.2, R28.2, SW1.1, SW1.2; also elsewhere on the board
NRST: C62.1, SW1.3 (K), SW1.4 (A); also elsewhere on the board

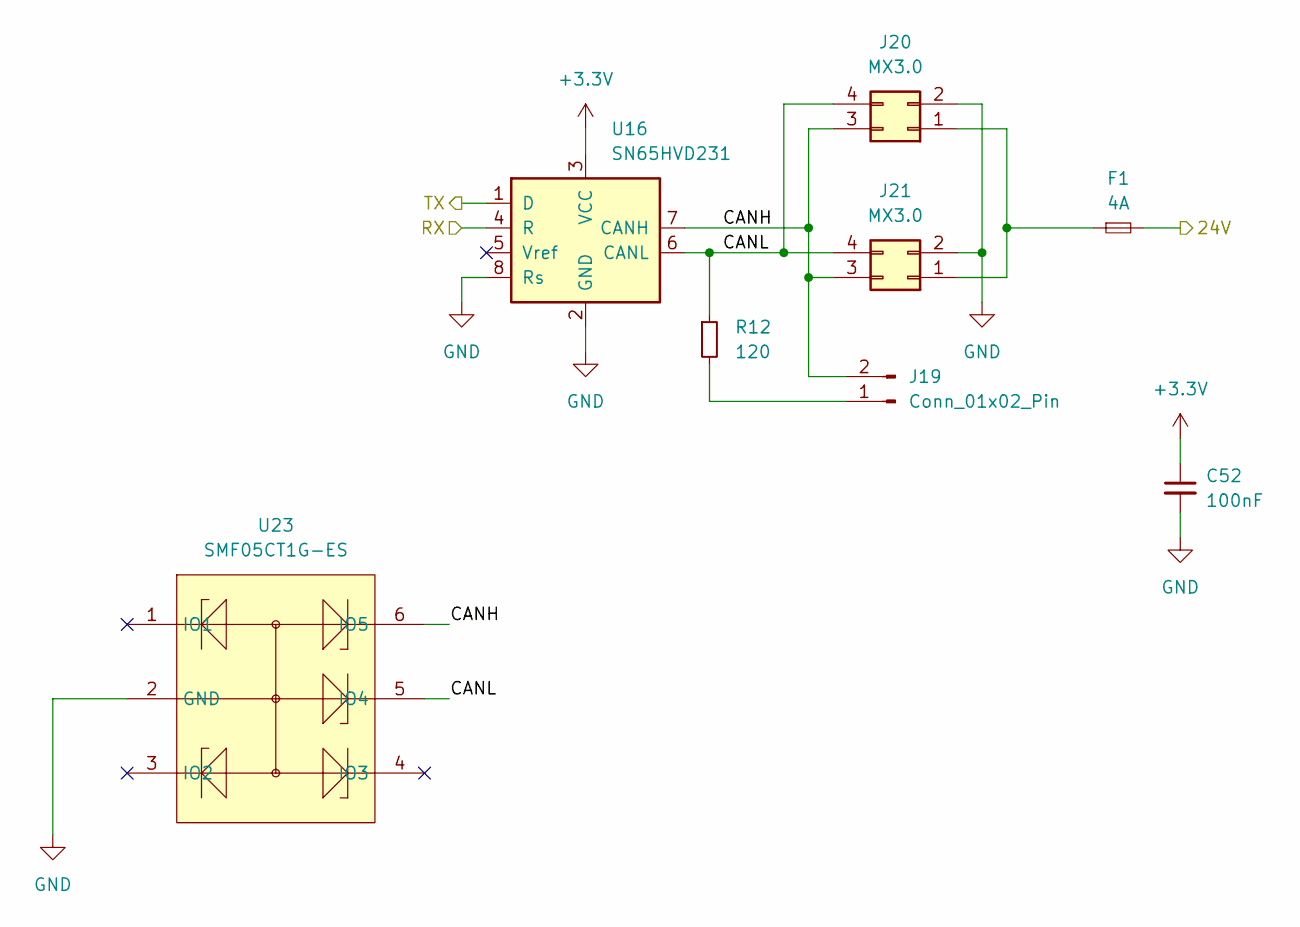
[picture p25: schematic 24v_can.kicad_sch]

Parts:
C52: 100nF; C_0603_1608Metric
F1: 4A; Fuseholder_Littelfuse_Nano2_154x
J19: Conn_01x02_Pin; PinHeader_1x02_P2.54mm_Vertical
J20, J21: MX3.0; Molex_Micro-Fit_3.0_43045-0412_2x02_P3.00mm_Vertical
R12: 120; R_0603_1608Metric
U16: SN65HVD231; SOIC-8_3.9x4.9mm_P1.27mm
U23: SMF05CT1G-ES; SOT-363_SC-70-6; LCSC Part C5180312

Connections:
+3.3V: C52.1, U16.3 (VCC); also elsewhere on the board
+24V: F1.2; also elsewhere on the board
/24V_CAN/CANH: J19.2, J20.3, J21.3, U16.7 (CANH), U23.6 (IO5)
/24V_CAN/CANL: J20.4, J21.4, R12.1, U16.6 (CANL), U23.5 (IO4)
CAN_RX: U16.4 (R); also elsewhere on the board
CAN_TX: U16.1 (D); also elsewhere on the board
GND: C52.2, J20.2, J21.2, U16.2 (GND), U16.8 (Rs), U23.2 (GND); also elsewhere on the board
unnamed: J19.1, R12.2
unnamed: F1.1, J20.1, J21.1

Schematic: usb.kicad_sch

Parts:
J42: JST-ZH; JST_ZH_B4B-ZR_1x04_P1.50mm_Vertical
U20: SMF05CT1G-ES; SOT-363_SC-70-6; LCSC Part C5180312

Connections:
GND: J42.4, U20.2 (GND); also elsewhere on the board
USB_DN: J42.2, U20.1 (IO1); also elsewhere on the board
USB_DP: J42.3, U20.6 (IO5); also elsewhere on the board
VBUS: J42.1, U20.5 (IO4); also elsewhere on the board

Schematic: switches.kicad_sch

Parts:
C14, C15: 100nF; C_0603_1608Metric
RN1, RN2, RN3, RN4: 10k; R_Array_Convex_4x0603
U2, U3: SN74LVC245APW; TSSOP-20_4.4x6.5mm_P0.65mm

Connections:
+3.3V: C14.1, C15.1, RN1.5 (R4.2), RN1.6 (R3.2), RN1.7 (R2.2), RN1.8 (R1.2), RN2.5 (R4.2), RN2.6 (R3.2), RN2.7 (R2.2), RN2.8 (R1.2), RN3.5 (R4.2), RN3.6 (R3.2), RN3.7 (R2.2), RN3.8 (R1.2), RN4.5 (R4.2), RN4.6 (R3.2), RN4.7 (R2.2), RN4.8 (R1.2), U2.1 (DIR), U2.20 (VCC), U3.1 (DIR), U3.20 (VCC); also elsewhere on the board
/Endstops/Switch 1/SW: U3.6 (A5); also elsewhere on the board
/Endstops/Switch 2/SW: U3.7 (A6); also elsewhere on the board
/Endstops/Switch 3/SW: U3.9 (A8); also elsewhere on the board
/Endstops/Switch 4/SW: U3.8 (A7); also elsewhere on the board
/Endstops/Switch 5/SW: U2.3 (A2); also elsewhere on the board
/Endstops/Switch 6/SW: U2.2 (A1); also elsewhere on the board
/Endstops/Switch 7/SW: U2.4 (A3); also elsewhere on the board
/Endstops/Switch 8/SW: U2.5 (A4); also elsewhere on the board
/Endstops/Switch 9/SW: U3.2 (A1); also elsewhere on the board
/Endstops/Switch 10/SW: U3.3 (A2); also elsewhere on the board
/Endstops/Switch 11/SW: U3.4 (A3); also elsewhere on the board
/Endstops/Switch 12/SW: U3.5 (A4); also elsewhere on the board
/Endstops/Switch 13/SW: U2.9 (A8); also elsewhere on the board
/Endstops/Switch 14/SW: U2.8 (A7); also elsewhere on the board
/Endstops/Switch 15/SW: U2.7 (A6); also elsewhere on the board
/Endstops/Switch 16/SW: U2.6 (A5); also elsewhere on the board
GND: C14.2, C15.2, U2.10 (GND), U2.19 (~OE), U3.10 (GND), U3.19 (~OE); also elsewhere on the board
SW1: RN4.1 (R1.1), U3.14 (B5); also elsewhere on the board
SW2: RN4.2 (R2.1), U3.13 (B6); also elsewhere on the board
SW3: RN4.3 (R3.1), U3.12 (B7); also elsewhere on the board
SW4: RN4.4 (R4.1), U3.11 (B8); also elsewhere on the board
SW5: RN1.2 (R2.1), U2.17 (B2); also elsewhere on the board
SW6: RN1.1 (R1.1), U2.18 (B1); also elsewhere on the board
SW7: RN1.3 (R3.1), U2.16 (B3); also elsewhere on the board
SW8: RN1.4 (R4.1), U2.15 (B4); also elsewhere on the board
SW9: RN3.1 (R1.1), U3.18 (B1); also elsewhere on the board
SW10: RN3.2 (R2.1), U3.17 (B2); also elsewhere on the board
SW11: RN3.3 (R3.1), U3.16 (B3); also elsewhere on the board
SW12: RN3.4 (R4.1), U3.15 (B4); also elsewhere on the board
SW13: RN2.4 (R4.1), U2.11 (B8); also elsewhere on the board
SW14: RN2.3 (R3.1), U2.12 (B7); also elsewhere on the board
SW15: RN2.2 (R2.1), U2.13 (B6); also elsewhere on the board
SW16: RN2.1 (R1.1), U2.14 (B5); also elsewhere on the board

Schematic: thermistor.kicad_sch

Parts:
C82: 100nF; C_0603_1608Metric
D32: BAV99; SOT-23
J50: Conn_01x02_Pin; JST_XH_B2B-XH-A_1x02_P2.50mm_Vertical
R108, R109: 2.37k; C_0603_1608Metric
R110: 4.7k; C_0603_1608Metric

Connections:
+3.3V: D32.2 (A), R110.2; also elsewhere on the board
GND: C82.1, D32.1 (K), J50.2; also elsewhere on the board
unnamed: D32.3 (K), R108.1, R109.2
unnamed: J50.1, R108.2, R110.1
TH0: C82.2, R109.1; also elsewhere on the board

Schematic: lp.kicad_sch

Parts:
D6: LED; LED_0603_1608Metric
D7: 1N4007; D_SOD-123
J41: Conn_01x02_Pin; JST_XH_B2B-XH-A_1x02_P2.50mm_Vertical
Q2: IRLML0030; SOT-23
R64: 2.7k; R_0603_1608Metric
R65: 100; R_0603_1608Metric
R66: 10k; R_0603_1608Metric

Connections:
+24V: D7.1 (K), J41.1; also elsewhere on the board
GND: Q2.2 (S), R64.1, R66.2; also elsewhere on the board
unnamed: D6.1 (K), R64.2
unnamed: D7.2 (A), J41.2, Q2.3 (D)
unnamed: Q2.1 (G), R65.2, R66.1
OUT2: D6.2 (A), R65.1; also elsewhere on the board

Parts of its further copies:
D9: LED; LED_0603_1608Metric
D10: 1N4007; D_SOD-123
J44: Conn_01x02_Pin; JST_XH_B2B-XH-A_1x02_P2.50mm_Vertical
Q4: IRLML0030; SOT-23
R70: 2.7k; R_0603_1608Metric
R71: 100; R_0603_1608Metric
R72: 10k; R_0603_1608Metric

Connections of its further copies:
+24V: D10.1 (K), J44.1; also elsewhere on the board
GND: Q4.2 (S), R70.1, R72.2; also elsewhere on the board
unnamed: D9.1 (K), R70.2
unnamed: D10.2 (A), J44.2, Q4.3 (D)
unnamed: Q4.1 (G), R71.2, R72.1
OUT3: D9.2 (A), R71.1; also elsewhere on the board

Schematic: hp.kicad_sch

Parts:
D5: LED; LED_0603_1608Metric
J39: Conn_01x02_Pin; Molex_Micro-Fit_3.0_43045-0212_2x01_P3.00mm_Vertical
Q1: HY1904C2; DFN-8_L5.9-W5.2-P1.27-LS6.2-BL; LCSC Part C358116
R61: 3.3k; R_0603_1608Metric
R62: 100; R_0603_1608Metric
R63: 10k; R_0603_1608Metric

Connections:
+24V: J39.1; also elsewhere on the board
/Outputs/High Power 1/EN: D5.2 (A), R62.1; also elsewhere on the board
GND: Q1.1 (S), Q1.2 (S), Q1.3 (S), R61.1, R63.2; also elsewhere on the board
unnamed: D5.1 (K), R61.2
unnamed: J39.2, Q1.5 (D), Q1.6 (D), Q1.7 (D), Q1.8 (D), Q1.9 (D)
unnamed: Q1.4 (G), R62.2, R63.1

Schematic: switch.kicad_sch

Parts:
C63: 100nF; C_0603_1608Metric
D15: LED; LED_0603_1608Metric
J23: JST-XH; JST_XH_B3B-XH-A_1x03_P2.50mm_Vertical
R29: 100k; R_0603_1608Metric
R30: 100; R_0603_1608Metric
R79: 3.3k; R_0603_1608Metric

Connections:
+5V: D15.2 (A), J23.3, R29.1; also elsewhere on the board
/Endstops/Switch 16/SW: R30.2, R79.1; also elsewhere on the board
GND: C63.2, J23.2; also elsewhere on the board
unnamed: D15.1 (K), R79.2
unnamed: C63.1, J23.1, R29.2, R30.1

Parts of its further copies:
C64, C65, C66, C67, C68, C69, C70, C71, C72, C73, C74, C75, C76, C77, C78: 100nF; C_0603_1608Metric
D16, D17, D18, D19, D20, D21, D22, D23, D24, D25, D26, D27, D28, D29, D30: LED; LED_0603_1608Metric
J24, J25, J26, J27, J28, J29, J30, J31, J32, J33, J34, J35, J36, J37, J38: JST-XH; JST_XH_B3B-XH-A_1x03_P2.50mm_Vertical
R31, R33, R35, R37, R39, R41, R43, R45, R47, R49, R51, R53, R55, R57, R59: 100k; R_0603_1608Metric
R32, R34, R36, R38, R40, R42, R44, R46, R48, R50, R52, R54, R56, R58, R60: 100; R_0603_1608Metric
R80, R81, R82, R83, R84, R85, R86, R87, R88, R89, R90, R91, R92, R93, R94: 3.3k; R_0603_1608Metric

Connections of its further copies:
+5V: D16.2 (A), D17.2 (A), D18.2 (A), D19.2 (A), D20.2 (A), D21.2 (A), D22.2 (A), D23.2 (A), D24.2 (A), D25.2 (A), D26.2 (A), D27.2 (A), D28.2 (A), D29.2 (A), D30.2 (A), J24.3, J25.3, J26.3, J27.3, J28.3, J29.3, J30.3, J31.3, J32.3, J33.3, J34.3, J35.3, J36.3, J37.3, J38.3, R31.1, R33.1, R35.1, R37.1, R39.1, R41.1, R43.1, R45.1, R47.1, R49.1, R51.1, R53.1, R55.1, R57.1, R59.1; also elsewhere on the board
/Endstops/Switch 1/SW: R60.2, R94.1; also elsewhere on the board
/Endstops/Switch 2/SW: R56.2, R92.1; also elsewhere on the board
/Endstops/Switch 3/SW: R48.2, R88.1; also elsewhere on the board
/Endstops/Switch 4/SW: R52.2, R90.1; also elsewhere on the board
/Endstops/Switch 5/SW: R44.2, R86.1; also elsewhere on the board
/Endstops/Switch 6/SW: R40.2, R84.1; also elsewhere on the board
/Endstops/Switch 7/SW: R36.2, R82.1; also elsewhere on the board
/Endstops/Switch 8/SW: R32.2, R80.1; also elsewhere on the board
/Endstops/Switch 9/SW: R58.2, R93.1; also elsewhere on the board
/Endstops/Switch 10/SW: R54.2, R91.1; also elsewhere on the board
/Endstops/Switch 11/SW: R50.2, R89.1; also elsewhere on the board
/Endstops/Switch 12/SW: R46.2, R87.1; also elsewhere on the board
/Endstops/Switch 13/SW: R42.2, R85.1; also elsewhere on the board
/Endstops/Switch 14/SW: R38.2, R83.1; also elsewhere on the board
/Endstops/Switch 15/SW: R34.2, R81.1; also elsewhere on the board
GND: C64.2, C65.2, C66.2, C67.2, C68.2, C69.2, C70.2, C71.2, C72.2, C73.2, C74.2, C75.2, C76.2, C77.2, C78.2, J24.2, J25.2, J26.2, J27.2, J28.2, J29.2, J30.2, J31.2, J32.2, J33.2, J34.2, J35.2, J36.2, J37.2, J38.2; also elsewhere on the board
unnamed: D16.1 (K), R80.2
unnamed: D17.1 (K), R81.2
unnamed: D18.1 (K), R82.2
unnamed: D19.1 (K), R83.2
unnamed: D20.1 (K), R84.2
unnamed: D21.1 (K), R85.2
unnamed: D22.1 (K), R86.2
unnamed: D23.1 (K), R87.2
unnamed: D24.1 (K), R88.2
unnamed: D25.1 (K), R89.2
unnamed: D26.1 (K), R90.2
unnamed: D27.1 (K), R91.2
unnamed: D28.1 (K), R92.2
unnamed: D29.1 (K), R93.2
unnamed: D30.1 (K), R94.2
unnamed: C64.1, J24.1, R31.2, R32.1
unnamed: C65.1, J25.1, R33.2, R34.1
unnamed: C66.1, J26.1, R35.2, R36.1
unnamed: C67.1, J27.1, R37.2, R38.1
unnamed: C68.1, J28.1, R39.2, R40.1
unnamed: C69.1, J29.1, R41.2, R42.1
unnamed: C70.1, J30.1, R43.2, R44.1
unnamed: C71.1, J31.1, R45.2, R46.1
unnamed: C72.1, J32.1, R47.2, R48.1
unnamed: C73.1, J33.1, R49.2, R50.1
unnamed: C74.1, J34.1, R51.2, R52.1
unnamed: C75.1, J35.1, R53.2, R54.1
unnamed: C76.1, J36.1, R55.2, R56.1
unnamed: C77.1, J37.1, R57.2, R58.1
unnamed: C78.1, J38.1, R59.2, R60.1

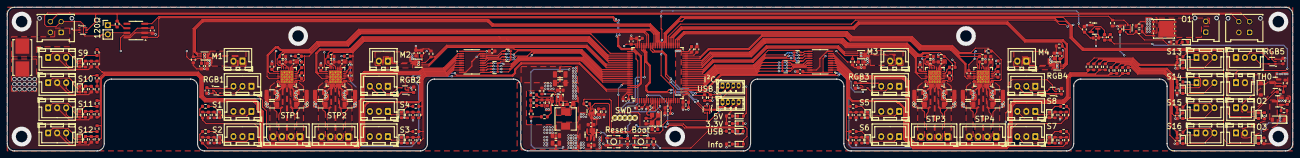
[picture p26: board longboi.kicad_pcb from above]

Board: 4 copper layers, 358.0 x 40.0 mm, 288 parts (0 on the bottom side), 213 nets.

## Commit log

2025-06-17 add cad add stl reorganize pcb design files
    [24v_can.kicad_sch, fan.kicad_sch, heater.kicad_sch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]
2025-06-17 ignore lock files add katapult/klipper reference config
2025-06-17 add klipper board alias cfg
    [longboi.cfg]
2025-06-20 add pcb step file
2025-06-25 fixes #3: increased input/output capacitor values for ME6211C33M5
    [longboi.kicad_sch, outputs.kicad_sch, regulators.kicad_sch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]
2025-06-25 fixes #2: changed resistor divider values
    [regulators.kicad_sch]
2025-06-25 fixes #8: changed led series resistor values
    [hp.kicad_sch, longboi.kicad_sch, lp.kicad_sch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]
2025-06-29 update pcb
    [longboi.kicad_pcb]
2025-08-30 fixes #9 fixes #4 fixes #13
    [24v_can.kicad_sch, longboi.kicad_pcb]
2025-08-31 fixes #6
    [hp.kicad_sch, longboi.kicad_pcb, lp.kicad_sch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]
2025-09-02 fixes #15
    [longboi.kicad_pcb, longboi.kicad_sch, outputs.kicad_sch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]
2025-09-02 fixes #5
    [longboi.cfg, longboi.kicad_pcb, switches.kicad_sch]
2025-09-02 fixes #10
    [longboi.kicad_pcb, motor.kicad_sch]
2025-09-02 fixes #12
    [longboi.kicad_pcb, switches.kicad_sch]
2025-09-25 fixes #7
    [longboi.kicad_sch]
2025-10-23 specified some values and colors added lcsc part ids for all components
    [24v_can.kicad_sch, hp.kicad_sch, longboi.kicad_sch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]
2025-11-03 fixes #16
    [longboi.cfg]
2025-11-12 fix wrong lcsc id for crystal cover up swapped net for sw3 and sw4 by swapping in config
    [longboi.cfg, longboi.kicad_sch]
2025-11-12 refactor image material
2025-11-12 update gerber files
    [longboi-B_Cu.gbr, longboi-B_Mask.gbr, longboi-B_Paste.gbr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]
2025-11-24 spacer reoriented for printing
    [pcb_spacer_x7.stl]
2025-11-24 re-export cad + stl with correct orientation and unit
    [pcb_spacer.step, pcb_spacer_x7.stl, skirt_front_hex_single.step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]
2025-12-18 refactored cad/stl structure added step and stl files for BTE mounting
    [hex_front_left.stl, hex_front_right.stl, pcb_spacer.step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]
2026-01-08 fixes #20 fixes #22 fixes #19
    [bom.csv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]
2026-01-09 fix tmc2209 position in placement file
    [positions.csv]
